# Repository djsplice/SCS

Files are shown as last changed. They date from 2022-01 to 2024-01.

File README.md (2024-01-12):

# Super Cooling System
This work is based on the [VzBoT RSCS system](https://grabcad.com/library/rscs-for-vzbot-1). Big thanks to the VzBoT crew, especially [Simon Vezina](https://grabcad.com/simon.vezina-2) for providing all of the CAD drawings and awesome videos for information, inspiration, and acceleration!

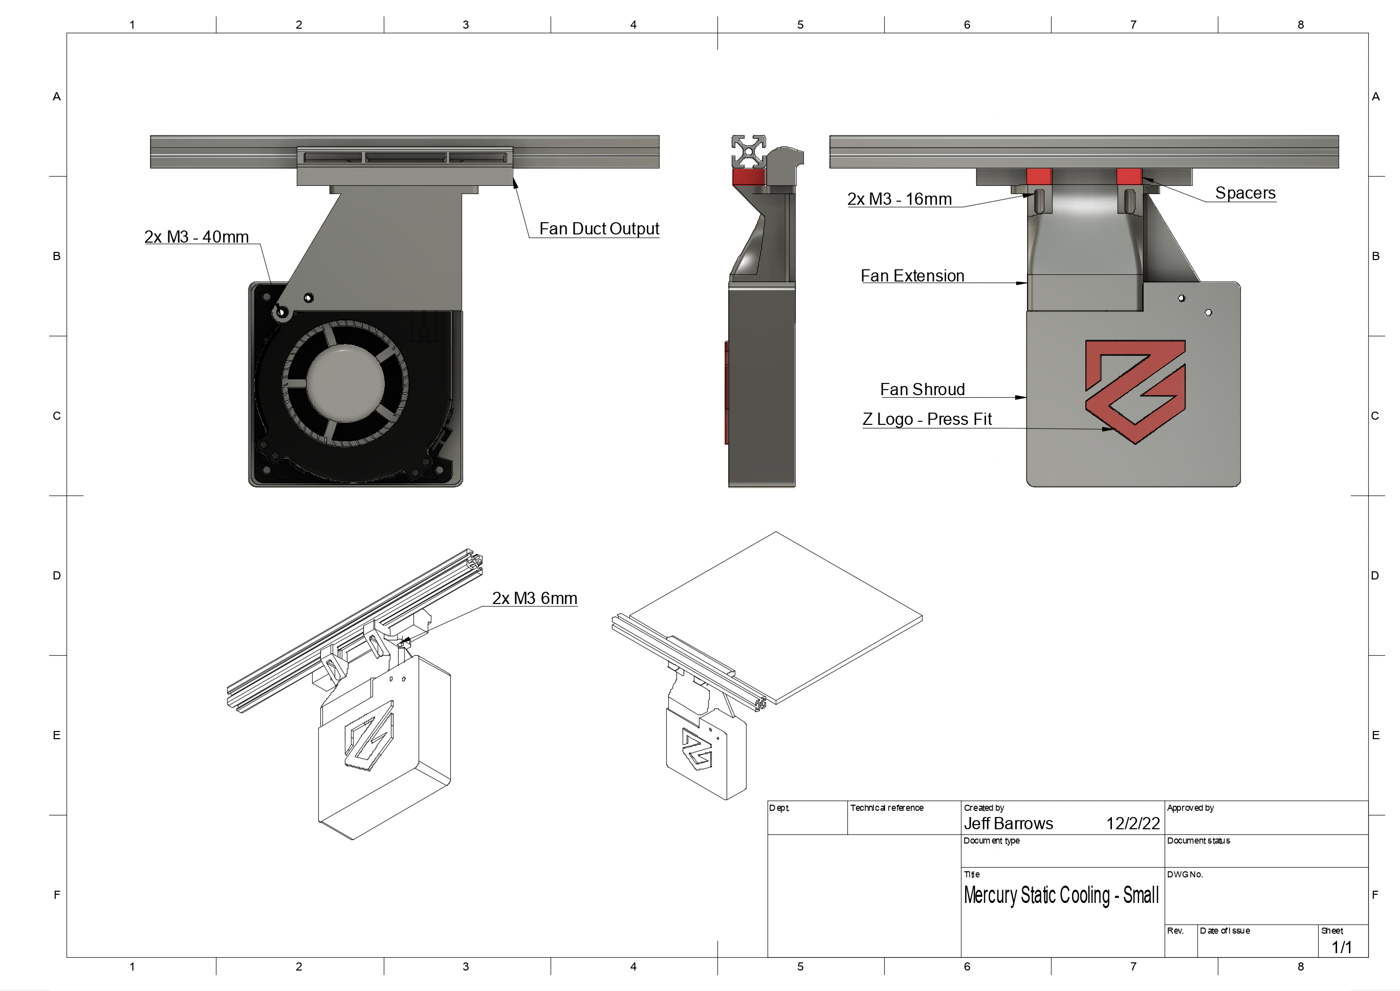
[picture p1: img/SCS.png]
Much SCS


## Release History
* 12/04/22 - Improved fan bracket airflow, and eliminated the need for the extension. Made shorter duct and increased inner cavity for improved airflow. Added a 'press-fit' Z for some flair.
* 7/11/22 - Updated fan bracket and shroud to cover more of the fans output. Increase overall fan bracket thickness improving mounting stability. Thanks to dansxmods#0246 (ZeroG Discord Server) for the suggestion!
* 5/26/22 - Initial Release

## What's SCS?
This is a system that's meant to cool top layer 3D printed extrusions quickly, helping you up the brrrr with better quality prints.

### What's the problem?
I found that as I tried to print at the higher end of my printers mechanical and extruder capabilities inevitably my print quality would suffer.  Especially challenging were overhangs, even 45 degree outer layers, and models with short layer print times (smaller single parts).

I moved to a dual 5015 cooling setup (EVA) for my part cooling which helped though at higher volumetric flows (~17mm3/sec), certain model features would become problematic (Benchy bow sag, ~45-50 degree overhangs in vase mode would deform at moderate speed, etc... ).

After watching and tuning for these scenarios it became clearer that cooling solutions that travel with the hot end have their limits. I think the main challenge is in that when printing at low layer times (<3sec), the fan ducts are generally not providing adequate cooling to the parts top layer surface because the hot end cooling fan is directly focused over the traveling nozzle.

More science necessary, though I believe cooling time could be calculated for a given material - helpful in determining quality print speed.

### Why try the SCS?
**First** I want to mention that the only reason I have this cooling problem is largely due to the [Zero-G Mercury project](https://github.com/ZeroGDesign/Mercury). By converting my heretofore fairly well tuned Ender 5 Pro printing at ~75mm/sec into something more 'moderately dangerous' - currently approaching 350mm/sec and 40mms3 volumetric flow.

After watching the [VzBoT video](https://youtu.be/65FVQ1jArME) on cooling solutions I was convinced to try this myself.

My hypothesis is that by adding additional top layer cooling, you'll be able to achieve higher speed/higher quality 3D prints.

If you're game, help me evaluate!

## SCS Parts, Printing, Installation
All printed files are found in the STL folder, CAD files *soon

This design works for the Ender 5 Pro, just fits between the top 2020 extrusion and a 300mm bed. If you have a smaller bed, or the Ender 5 Plus it should fit, though for the plus it may be a bit too far away from the bed, or not provide great part coverage... Drop an issue in Github if you get a chance to test it!

You will need M3 screws, 2 fans, and the ability to print 15mm overhangs clearly - you can do it - or your money back!   

### Hardware
* 2x 120x32 centrifugal fans - make sure they match the voltage and pin configuration your board can work with!
 * Ability to crimp, solder, or otherwise connect the fans to your 3D printer controller board
* Various M3 bolts/nuts:
 * 2x 40mm bolts to affix fan and shroud to mount
 * 2x 6mm M3 bolts to connect the fan shroud to the fan extension
 * 2x 16mm M3 bolts to connect the entire system to the underside of 2020 Aluminum extrusion
* Roll In Spring T-Nuts for mounting the blower to the top 2020 extrusions-  - something like [these](https://8020.net/fasteningmethods/hardware/tnuts/rollin/rollintnutwithballspring.html)

### Printed Parts
I recommend using the the following print settings:
* 3 Perimeters and 4 bottom/top solid layers
* 40% infill

All printed parts are included in the STL folder - there are 5 parts:

* [Fan Duct.stl](stl/Fan_Duct.stl)
* [Z-Insert.stl](stl/Z-Insert.stl)
* [Fan Bracket.stl](stl/Fan_Bracket.stl)
* [Fan Shroud.stl](stl/Fan_Shroud.stl)
* 2x [Spacers.stl](stl/Spacers.stl)

### Installation
1. Thread the M3 6mm screws that will be used to attach the fan duct, let the screws protude slightly from the top so it's easier to mount the duct later. The screws will thread directly into the duct housing - no nuts necessary.
1. Insert the M3 16mm screws that will be used to mount the system to the underside of the 2020 extrusion, thread the t-nuts
1. Using roll-in t-nuts will allow you to tilt the duct and get them inserted under the 2020 extrusion
1. Center the duct so that it's in the middle of your print bed
1. Once the duct is hanging from the 2020 extrusions, insert the spacers between the the extrusion and the duct mount, and tighten the bolts
1. Mount the Fan Duct Output on top of the Fan Extension.
3. Mount the fan and the shroud

The base of Fan Duct Output should align with the base of your print bed - the idea is for the air to blow onto the top layer of your print, if it's too high above the bed, it won't be as effective.

You may need to adjust the height of the spacers to achieve optimal alignment for your printer.
[TODO] Add a few more spacer sizes to accommodate

### Klipper gcode macro example
Configure Klipper to control the fans and expose a GCode macro so it can be controlled by your slicer.

#### Klipper Fan configuration
```
[output_pin Bed-Blower-R]
# BED BLOWER RIGHT
pin: PD12
pwm: true

[output_pin Bed-Blower-L]
# BED BLOWER LEFT
pin: PD13
pwm: true
```

#### Klipper GCode Macro
```
[gcode_macro BED_BLOWER]
gcode:
    # Use a default fan speed to off - expecting an INT as input
    {% set S = (params.S)|default(0)|float %}
    {% if S > 0 %}
        {% set S = (S/100) %}
    {% endif %}
    SET_PIN PIN=Bed-Blower-R VALUE={S}
    SET_PIN PIN=Bed-Blower-L VALUE={S}
```

Alternatively you can configure ports as `fan_generic`

```
[fan_generic Bed-Blower-R]
# BED BLOWER RIGHT
pin: PD12
max_power: 1.0
shutdown_speed: 0
off_below: 0.0
kick_start_time: 0.100

[fan_generic Bed-Blower-L]
# BED BLOWER LEFT
pin: PD13
max_power: 1.0
shutdown_speed: 0
off_below: 0.0
kick_start_time: 0.100

[gcode_macro BED_BLOWER]
gcode:
    # Use a default fan speed to off - expecting an INT as input
    {% set S = (params.S)|default(0)|float %}
    {% if S > 0 %}
        {% set S = (S/100) %}
    {% endif %}
   SET_FAN_SPEED FAN=Bed-Blower-R SPEED={S} 
   SET_FAN_SPEED FAN=Bed-Blower-L SPEED={S}

[gcode_macro M106]
rename_existing: M106.1
gcode:
  M106.1 { rawparams }
  {% set bed_blower_speed = params.S|float * 100/255 %}
  SET_FAN_SPEED FAN=Bed-Blower-R SPEED={ bed_blower_speed/100 }
  SET_FAN_SPEED FAN=Bed-Blower-L SPEED={ bed_blower_speed/100 }
```

#### Klipper Custom M106 Macro
This macro will set your SCS Fans to the same value your slicer sets the part cooling fans to, making it more dynamic. There are probably some advantages to having an 'always on' static setting, vs a dynamically adjusted setting such as this.

```
[gcode_macro M106]
rename_existing: M106.1
gcode:
  M106.1 { rawparams }
  {% set bed_blower_speed = params.S|float * 100/255 %}
  SET_PIN PIN=Bed-Blower-R VALUE={ bed_blower_speed/100 }
  SET_PIN PIN=Bed-Blower-L VALUE={ bed_blower_speed/100 }
```

### SuperSlicer custom gcode integration
In order to automatically turn on the SCS fans at a specific layer height, you need to add some custom `Before Layer Change G-code` section under the 'Printer Settings' in SuperSlicer.

```
; Set SCS fans to 40% when you reach the 3rd layer
{if layer_num == 2} BED_BLOWER S=40{endif}
```

## Known Issues

### Fan Duct Outlet
* Lots of bridging in this print!!  I tried to keep the bridge distance low, around 15mm or so... It's a bummer, but hopefully it's doable.

### Fan Bracket
* There are only 2 points to connect the fan to the bracket and it isn't as secure as I'd like. I'll probably look to add another mount point and potentially strengthen the hole on the point of the triangle...

## Experiments
Here are some pictures of benchys printed using the same g-code, but with  different cooling solutions.

Slicer configuration
2 Perimeters, 3 Top/Bottom solid
.2mm layer height
18% gyroid infill
Internal Perimeter Speed 250mm/s - External - 125mm/s
Max Volumetric Speed 43mm/s

1. Single 5015 Part cooling Fans at 100%
1. Dual 5015 Part cooling Fans at 100%
1. Dual 5015 Part cooling fans at 100% plus SCS fans at 100%

My interpretation of these results:
* Short layer times require increased cooling capacity
* Certain features (like overhangs) will degrade more than others when cooling isn't sufficient
* Layer times and cooling requirements are correlated - faster layer times will require more Cooling
* Prints that have more surface area may have a bit more time to cool before the next layer is applied, however, nozzle based cooling solutions will be less effective because they are only in a position to cool a section for a very short amount of time (as the filament is extruded from the nozzle)
* Smaller prints can benefit somewhat from increased nozzle based cooling systems because the ducts are likely to cover more surface area of the print for a more sustained period of time. Unfortunately smaller parts will likely have very short layer times and nozzle based cooling will probably not be sufficient   

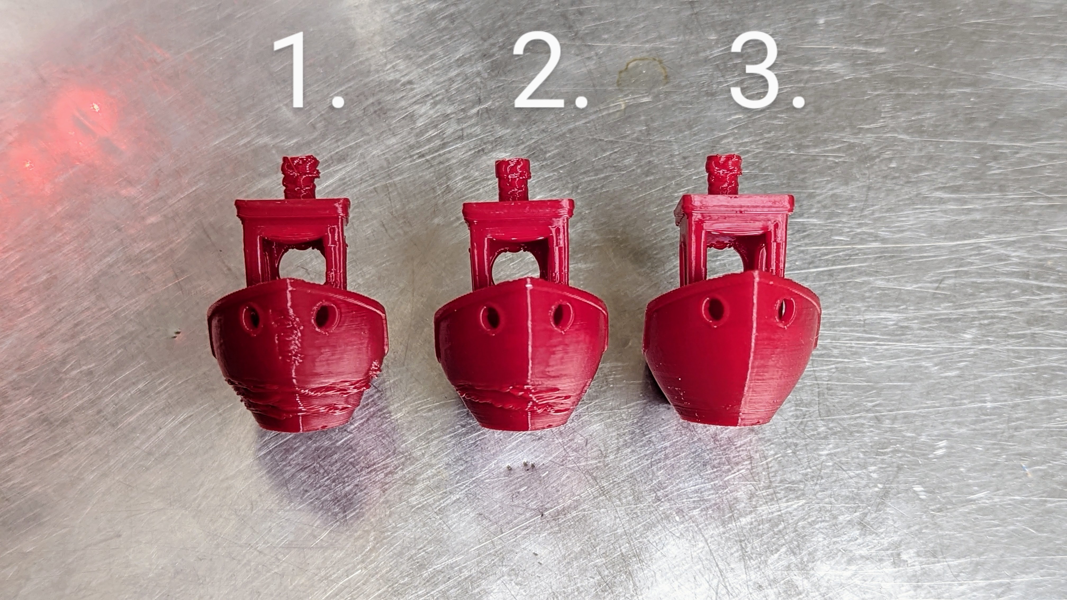
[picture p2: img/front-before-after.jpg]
Benchy Front View

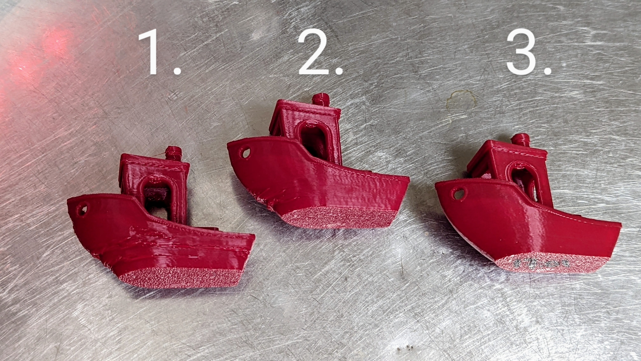
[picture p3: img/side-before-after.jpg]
Benchy Side View


### CFD Study
I found a nice [tutorial / overview](https://www.youtube.com/watch?v=Wun9EuVTV0w) from Teaching Tech that showed how to do some Computational Fluid Dynamics simulations using a site called [Simscale](https://www.simscale.com/). I quite literally have no idea if I'm using this tool correctly or not! With that said, it seems to provide some good visualizations of air flow, and reflects the changes I'd expect to see as I refined the CAD model.

Here is my [SimScale project](https://www.simscale.com/projects/djsplice/super_cooling_system_v2/), take the data for what it's worth - mostly for the neat visualization of airflow =)

It's been great to be able to make updates to a CAD model like this and run a simulation against the updated model to see if it has the intended effects - all before printing the part! Running the simulations take about an hour, so there's not tons of time savings, however, I do save quite a bit of filament!

#### V2 duct output design
Made some updates to the duct output in an attempt to better distribute the airflow across the bed, and keep it focused on the top layer of the print. It looks like the bed coverage has improved, perhaps at the cost of some velocity.  All good gains I think.

As much as I enjoy running simulations and updating CAD, I've decided to pause the iteration and get some real world print time under my belt with the current design as published here in GitHub.

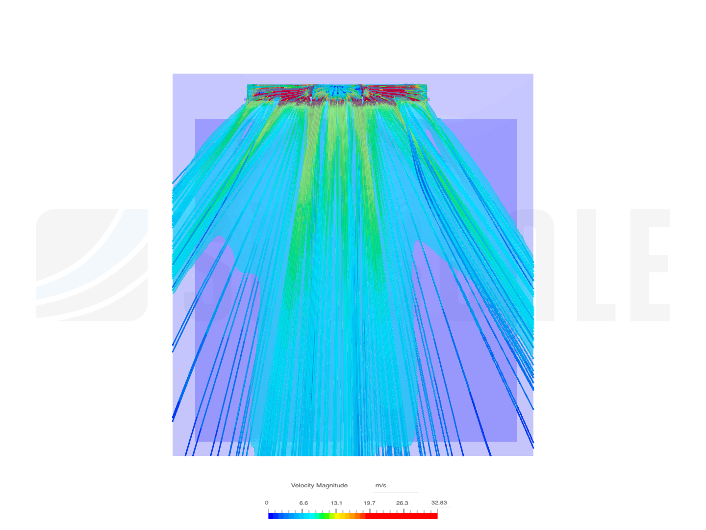
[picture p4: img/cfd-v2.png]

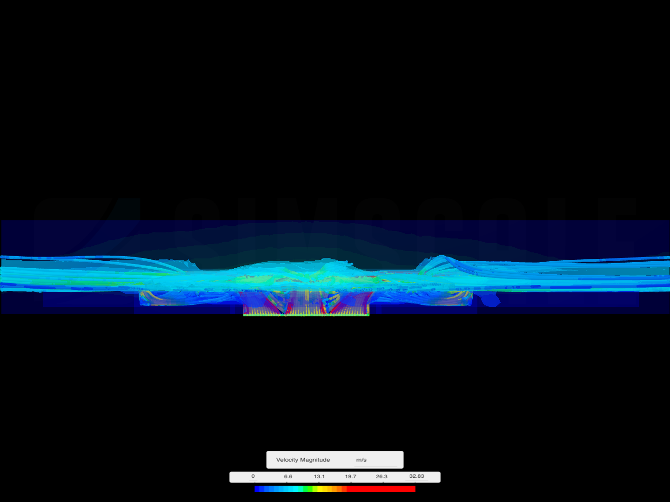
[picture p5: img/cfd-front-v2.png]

CFD v2 fan duct full plate

#### V1 duct output design
Some data to back up the physical observations (places hand in front of the vents). Looks like most of the air is flowing through the center of the duct, not much is getting to the outside edges...
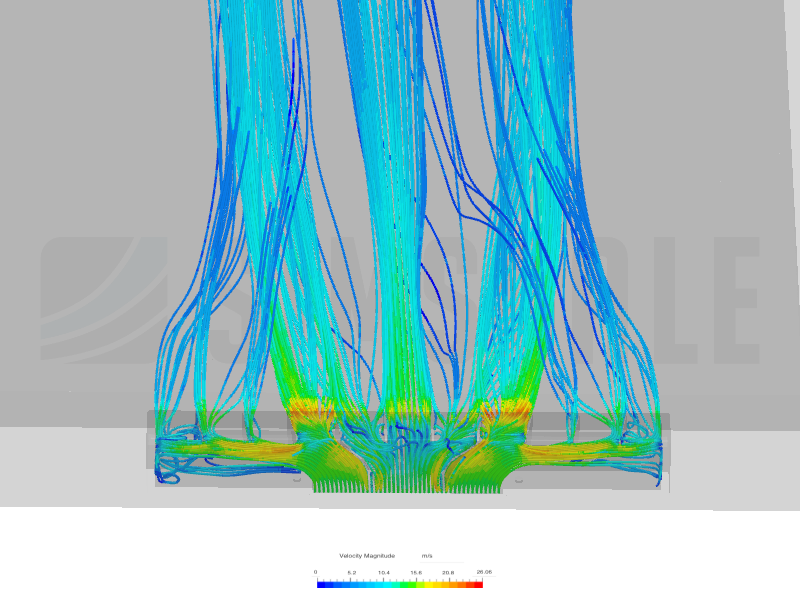
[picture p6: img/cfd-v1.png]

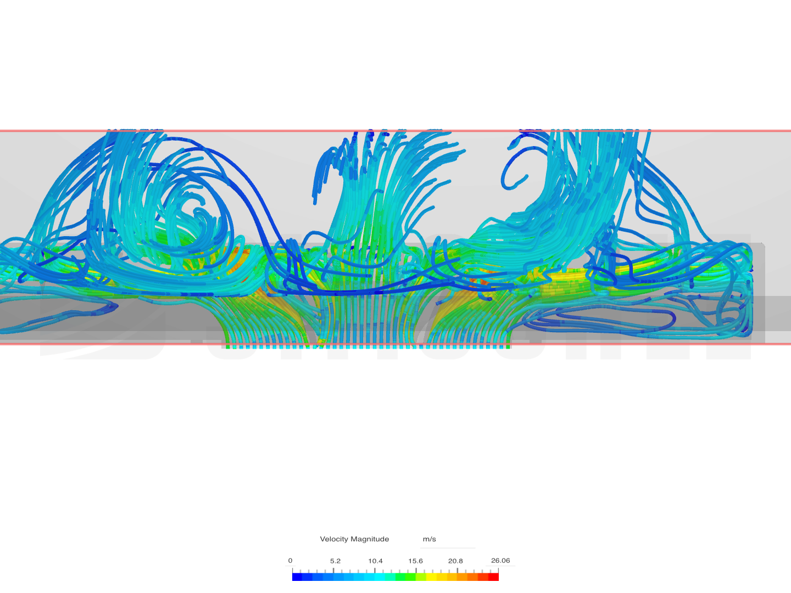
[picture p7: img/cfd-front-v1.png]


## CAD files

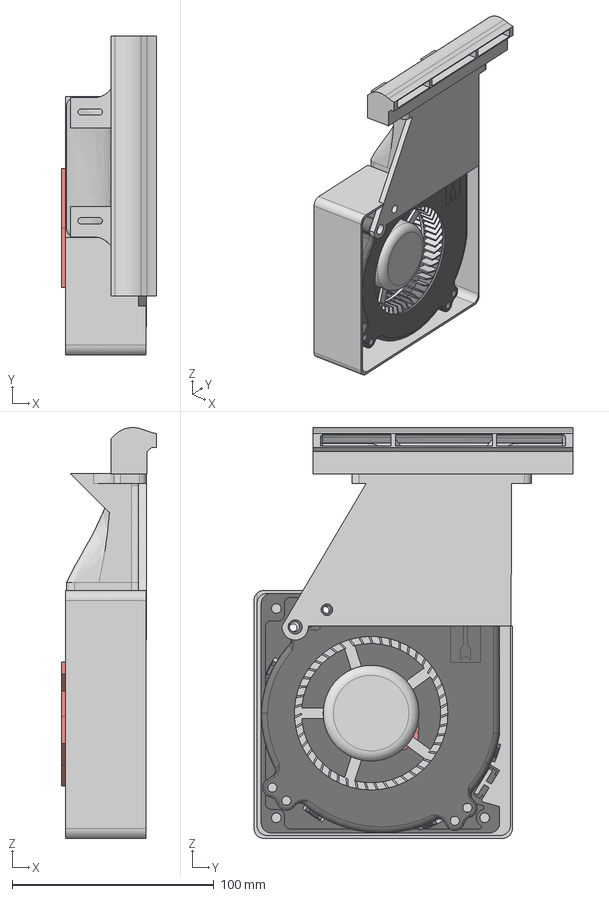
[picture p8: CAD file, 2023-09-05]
step/Mercury Static Cooling - Small.step
47.1 x 158.2 x 203.9 mm
Mercury Static Cooling Duct Small
Fan Shroud
Mercury Static Cooling_Mounting Spacers

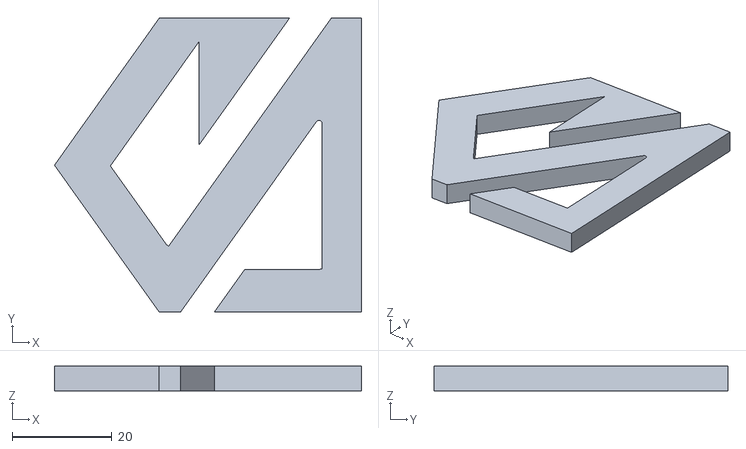
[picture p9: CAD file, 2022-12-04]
stl/Z-Insert.stl
61.6 x 59.0 x 5.00

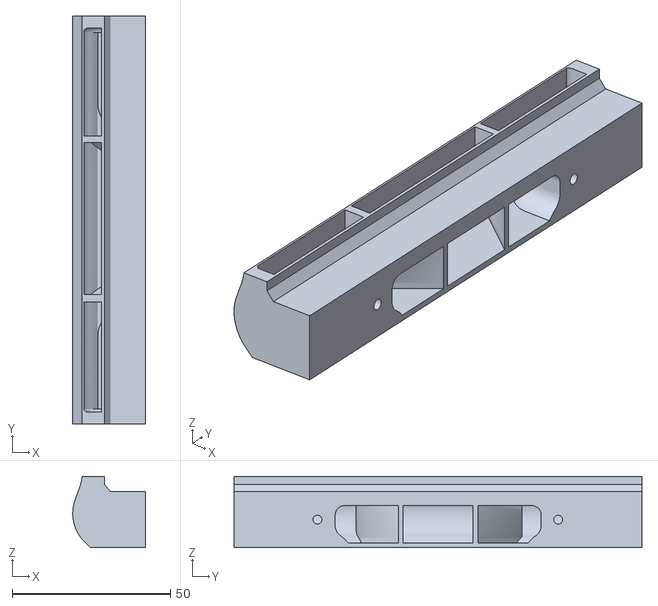
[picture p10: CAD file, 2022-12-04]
stl/Fan_Duct.stl
23.0 x 129.0 x 22.4

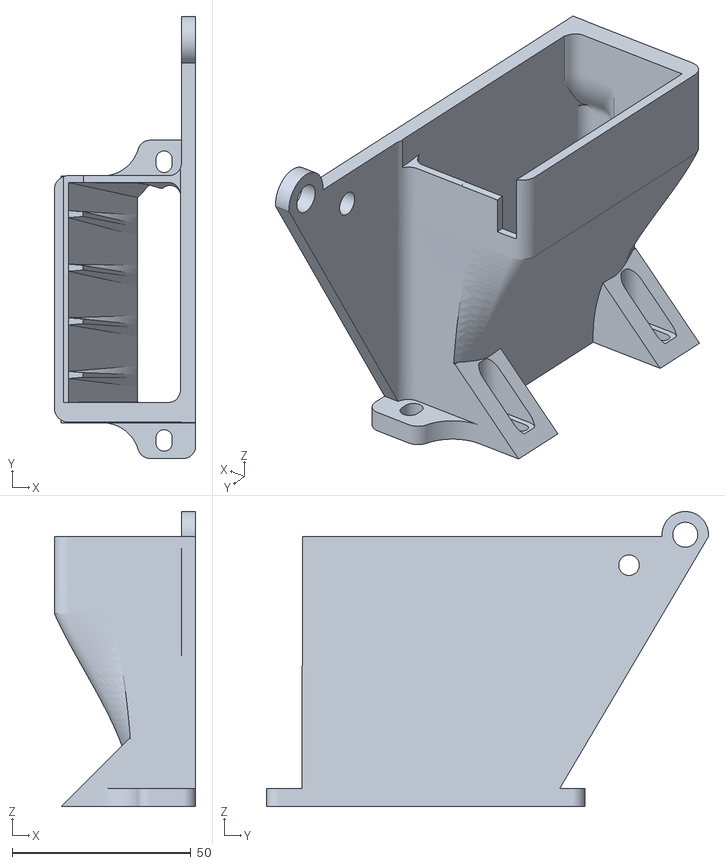
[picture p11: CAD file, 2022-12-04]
stl/Fan_Bracket.stl
39.6 x 123.7 x 82.6

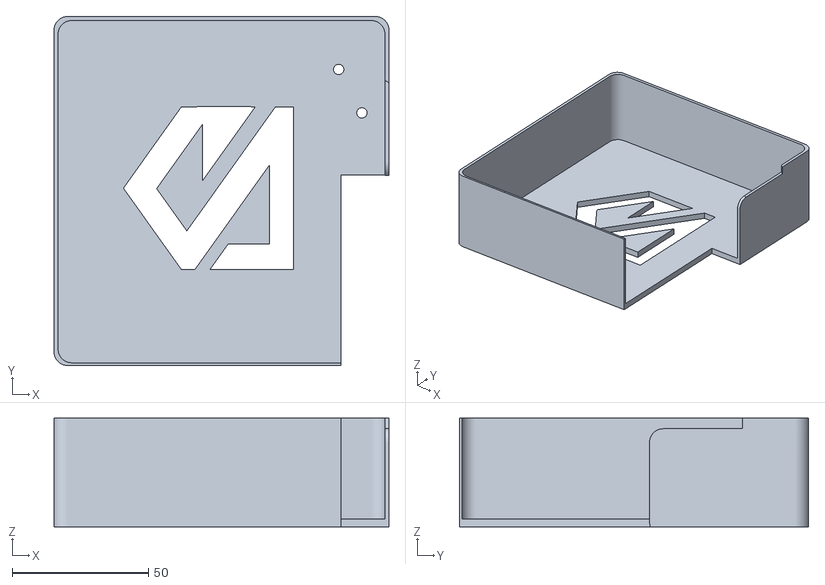
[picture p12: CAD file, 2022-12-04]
stl/Fan_Shroud.stl
123.1 x 128.2 x 40.0

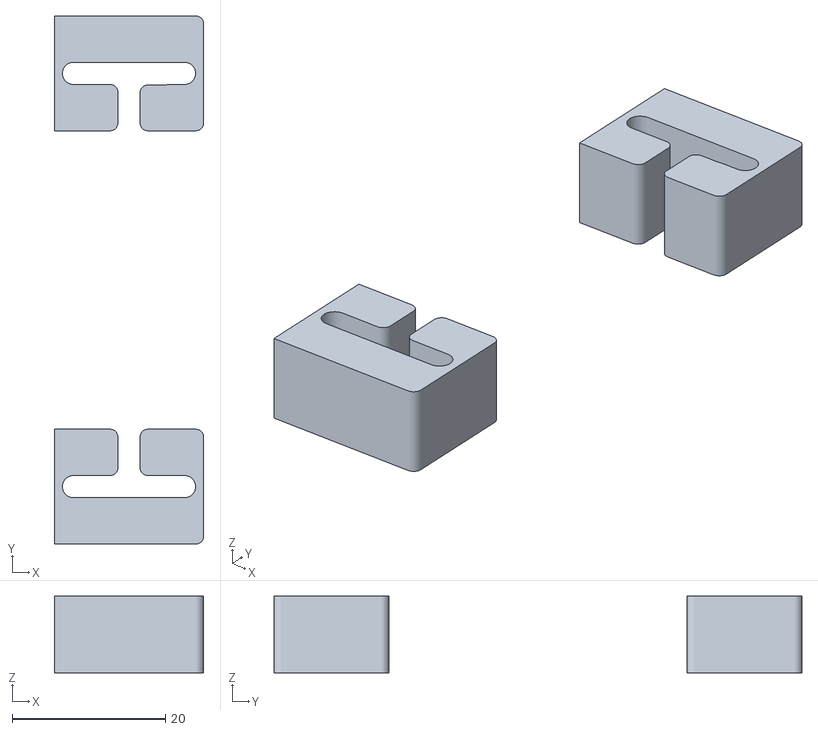
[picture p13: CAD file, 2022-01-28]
stl/Spacers.stl
19.5 x 69.0 x 10.0

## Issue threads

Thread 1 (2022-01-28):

See if you can improve air flow coverage from the fan duct output

djsplice, 2022-01-28:
Air flow seems to be more heavily concentrated in the center of the duct output. Flow on the outer edges is limited and is probably not that effective.

I think there's room for improvement here.

henrymaaaa, 2023-08-21:
I have been testing your v2 system and I have had success with correcting benchy sag, but I do not get any flow in the corners of the bed. Maybe if you reduce the duct height at the center it will reduce flow in the center and cause a more even distribution of flow to the edges of the duct.

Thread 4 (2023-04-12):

Issue Configuring

RobertoHernandezjr, 2023-04-12:
Tried setting up and got error I don't remember what it was but I think it has to do with the macro, I went ahead and just set it to generic fan and used  static airflow for now.  Curious what the advantage of using set pin vs generic fan, aslo SET_FAN_SPEED FAN=Bed-Blower-L SPEED=0.5 works since its a fan now.

djsplice, 2024-01-11:
Apologies - I didn't have email notifications setup on this repo!

Good question on the generic fan vs output pin - I think either should work, but you get some better options with generic fan.  I'll update the examples to reflect that! Thanks for the suggestion.

djsplice, 2024-01-11:
```
[fan_generic Bed-Blower-R]
# BED BLOWER RIGHT
pin: PD12
max_power: 1.0
shutdown_speed: 0
off_below: 0.0
kick_start_time: 0.100

[fan_generic Bed-Blower-L]
# BED BLOWER LEFT
pin: PD13
max_power: 1.0
shutdown_speed: 0
off_below: 0.0
kick_start_time: 0.100

[gcode_macro BED_BLOWER]
gcode:
    # Use a default fan speed to off - expecting an INT as input
    {% set S = (params.S)|default(0)|float %}
    {% if S > 0 %}
        {% set S = (S/100) %}
    {% endif %}
   SET_FAN_SPEED FAN=Bed-Blower-R SPEED={S}
   SET_FAN_SPEED FAN=Bed-Blower-L SPEED={S}

[gcode_macro M106]
rename_existing: M106.1
gcode:
  M106.1 { rawparams }
  {% set bed_blower_speed = params.S|float * 100/255 %}
  SET_FAN_SPEED FAN=Bed-Blower-R SPEED={ bed_blower_speed/100 }
  SET_FAN_SPEED FAN=Bed-Blower-L SPEED={ bed_blower_speed/100 }
```

Closed 2024-01-11.

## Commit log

2022-01-28 Much cooling
    [Bed Duct Output - 175mm.stl, Fan Bracket.stl, Fan Shroud.stl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]
2022-01-29 Rename Fan Duct STL
    [Fan Duct.stl]
2022-01-31 Updated Fan Duct for more even bed coverage, added CFD study
    [Fan Duct.stl]
2022-02-01 next iteration of Fan Duct
    [Fan Duct.stl]
2022-02-02 Updated Fan Duct with CFD analysis
    [Fan Duct.stl]
2022-02-05 Added latest fan duct design
    [Fan Duct.stl]
2022-02-18 Update README.md
    Corrected Fan Size
2022-07-12 Fix links after file rename
    [Fan Bracket.stl, Fan Duct.stl, Fan Shroud.stl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]
2022-12-04 Updated ducts, Brackets, Shroud
    [Fan_Bracket.stl, Fan_Duct.stl, Fan_Shroud.stl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]
2023-07-12 Delete Fan_Extension.stl
    No longer needed for this version of the SCS
2023-09-05 Added step file based on v14 of the small fan duct
    [Mercury Static Cooling - Small.step]
